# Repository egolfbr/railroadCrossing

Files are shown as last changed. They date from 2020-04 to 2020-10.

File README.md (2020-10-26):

# RailRoadCrossing
Arduino based railroad crossing replica 
## Table of Contents
## Table of Contents
**[Introduction](#Introduction)**<br>
**[Gather Materials](#Gather-Matierals)**<br>
**[Building](#Building)**<br>
**[Programming](#Programming)**<br>
**[Conclusion](#Conclusion)**<br>

## Introduction
With the coronavirus sending students home for the rest of the semester (spring 2020), I found myself with a lot of extra time on my hands and lots of parts that I have never used.I recalled that the theme for this years VBS at my church is a railroad theme and my idea was born. I decided that I was going to make a railroad crossing signal. You know the ones with the moving arm, sound and blinking lights. It seemed a little easy especially since I am a junior electrical engineering student so I set off to work, needless to say, I encountered many errors and problems that made this a not an “easy” project. Certainly not a “plug and go” anyway lets get started.

## Gather Materials
Step 1: Gather materials. 
* 3x Arduino UNOs - $23/ea (arduino.cc)
* 2x microswitches - $2/ea* (microcenter)
* 2x pushbuttons - $0.10/ea (digikey)
* 2x 8Ohm-1W speakers - $2.95/ea (microcenter)
* 1x adafruit sound effects board $30/ea (adafruit)
* 2x neopixel ring (16LEDs)
* 1x barrel jack
* 1x 5V 3A power supply
* 2x 10K ohm resistors
* Jumper wire
* 2x MOSFET N-ch 30V transistor
* 2x MOSFET P-ch 27A transistor
* 1x 555 timer
* 1x 125V 3A fuse
* 2x 10000pf ceramic capacitor
* 2x 1n4004 diode
* 1x 19rpm economy brush pur motor
* 1x 4mm shaft mount 32 pitch 16T gear
* 1x 32 pitch 64T 1” bore gear

Estimated total cost:
	For those who do not have any previous material the estimated total cost is about $276. This does not include shipping and tax as you will most likely end up ordering from multiple different places. Websites such as Amazon may make it cheaper. I ended up spending just under $100 on parts that I didn’t have. PCB ordering is also not factored into this cost. I usually order PCBs from China. This means that I have to order a minimum of 10 boards per design. Thus with SeedStudio, I will have to pay around $5 for each design as well as shipping and tax for each one. I also included what the cost would be had I been contracted by a client to build this device. I used a simple google search of the median income of an electrical engineer to base my calculation for the per hour pay. 

You may be wondering why I use so many microcontrollers for a relatively simple process. I was limited by 2 main factors in this build, materials that I had, and money. Now, using 3 micro controllers seems like a costly thing to do and it is. However, I was lucky enough to receive a donation of parts last year which included about 10 arduinos. So having these extra controllers was a huge relief because it allowed me to make this project more parallel. In other words, I have multiple processes running at the same time across multiple devices. I will get into this more as I explain the circuit in the next section, but as some of you may guess, running certain processes takes time and if I want to say blink LEDs and move a motor at the same time, there will be a delay in the circuit. I may make a video example of what I am talking about for those who are confused. 
## Building 
Step 2: build the circuit.
	The most important thing to remember here is to CONNECT ALL GROUND PINS. Also pin numbers are arbitrary. There is no specific reason I choose any of the digital IO pins. The SDA and SCL pins however must remain on A4 and A5 respectively. There are other places to connect these pins on other versions of the arduino UNO but I like to use these pins because they are universal on the UNO models. 
	Additionally, due to my lack of knowledge in EAGLE I will attach hand drawn circuit schematics for parts of the circuit that parts aren’t readily available for on EAGLE so that you have them and I will work on updating the EAGLE file so that there is one complete schematic file that can be downloaded. On the hand-drawn circuits, any node names that are the same on the EAGLE file are connected. For example, on the board labeled SOUND, there is a pin labeled SOUNDPIN. On the hand-drawn schematic there is also a SOUNDPIN, that means that those nodes are connected. Also there is a portion of the circuit that is simplified. For the neopixel rings I only included 2xsingle LED schematics. In reality each of those single LEDs is a whole 16 LED ring. Connections are the same though because you are connecting the last LED on the first ring with the first LED on the second ring.
	So like I mentioned before, I chose to use multiple arduino so that I could make this a parallel design. The other option for me would be to use an FPGA since those are much easier to parallelize however, I did not have the equipment to debug that device. So that is why I ended up with lots of arduinos. First I was planning on just using two arduinos but found that trying to quickly change cases in the state machine (the code implementation that I will discuss next), this proved too slow. This is because in the code I called a function to flash the neopixel LEDs and this takes time. 
Let me take a break here and explain why I chose neopixel rings. Realistically I would’ve used lots of small 3-5mm LEDs and not these rings. That is because with the single diodes, you can simply connect and disconnect power to blink the LEDs. This would lead me to do a hardware implementation of the blinking lights. This can be done a couple ways. I saw a way to do it with a switching NPN transistor similar to the 2n2222 (please correct me if I am wrong). I imagine that this can be done with a crystal oscillator or a 555 timer circuit. I did have several 555 timers available to use but unfortunately I only had about 20 THT LEDs. So that is the main reason that I used the rings. I also find the rings brighter. The big downside is that they must remain plugged into the programmed pin (in my case pin 6). 
Okay so I grabbed a new arduino so that I could put a dedicated LED flashing code on it to flash during 3 of the 4 states of the state machine. Even though this one arduino is slower than the rest in terms of reading/displaying data on the SDA line, it is more acceptable because little kids love LEDs and who cares if the LEDs are on for a second or 2 longer than necessary. It is much more desirable and safer than say having the master arudino not read the digital pins while the motor is still running trying to push the arm higher and stalling the motor and maybe causing a fire. 
For the sound arduino I used the Adafruit sound effects board and some low powered speakers. This was the plug and go part of the project. There is a tutorial on how to use this board on Adafruit’s website which I will post a link to. The sound file is a simple MP3 that I downloaded for free (link below). You don’t have to include a sound portion to this project as it does get rather annoying but I always enjoy sound effects.
For the motor I just used the sound arduino because the sound doesn’t take a lot of time because it is just toggling a pin high and low. I used an attached link for the build of a custom H-bridge motor driver with variable speed and direction. The attached link had 95% of the circuit already designed so that was very helpful. The only portion that I personally designed and built was making it “programmable.” This means that instead of using a physical switch to change direction and to power the motor on and off, I used signals from the arduino dedicated to that function. The main issue is that I needed a SPDT switch that doesn’t require human interaction. Again, limited by supplies I landed on a 5V relay. A relay can be used similar to a 2n2222 transistor in that it can control higher voltage and amperage signals with a common 5V or 3.3V signal depending on the relay. In this case I didn’t need it to control a high voltage or current, just the fact that I needed it to be programmable. So the relay portion of the circuit controls the direction because for an H-bridge, if one side is connected to the power supply, and the other side is at ground, then the motor spins one way and if you switch those signals then you can make it spin the other way. To control the status of the motor (whether it is on or off) I simply used another N-Channel MOSFET transistor. Below are some images of the full circuit. First is the full motor dirver all wired up with a PWM signal and Hbridge, then just the PWM signal generator (555 timer circuit), then the master controller which takes inputs from sensors and buttons, the LED circuit which is just some neoPixel Rings, and finally, the audio circuit. I used an Adafruit sound effects board to shorten the project and bring the complexity down a bit.
<p align="center">
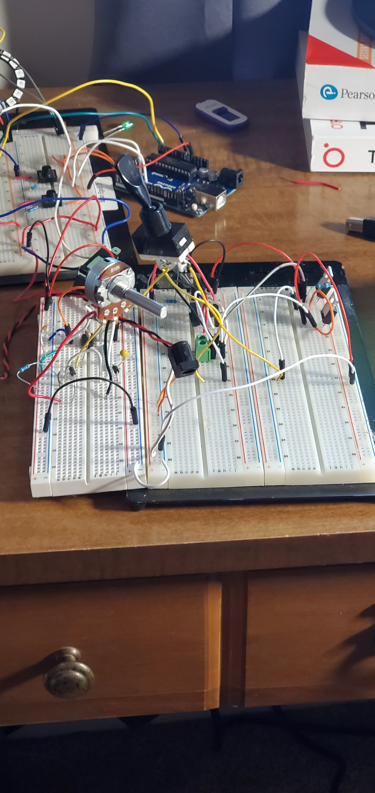
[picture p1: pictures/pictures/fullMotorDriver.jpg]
	
	
<p align="center">
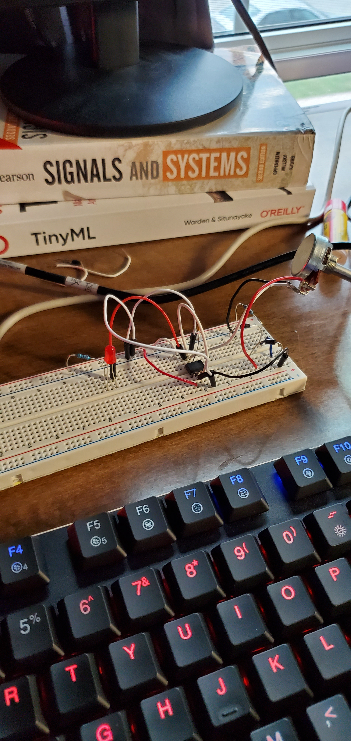
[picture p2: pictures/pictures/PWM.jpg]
		

<p align="center">
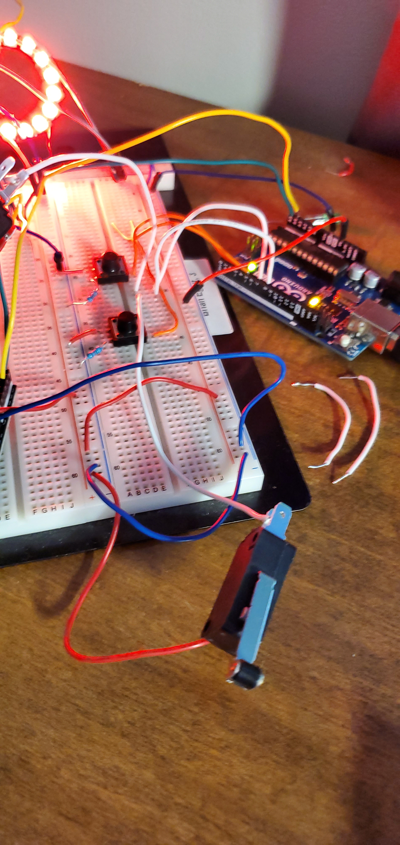
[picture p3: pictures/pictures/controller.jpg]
		

<p align="center">
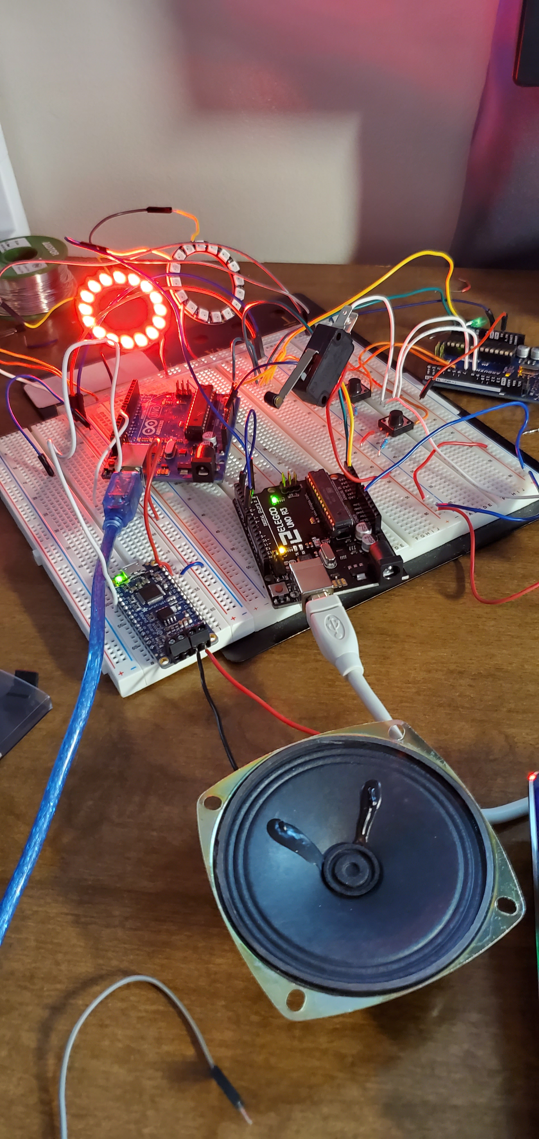
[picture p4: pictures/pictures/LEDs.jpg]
		

<p align="center">
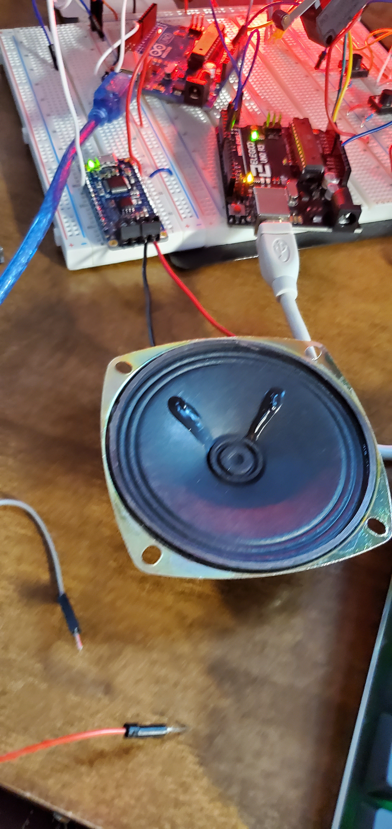
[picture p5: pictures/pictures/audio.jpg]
	

## Programming
Step 3: Code the Arduino’s
	For this project I implemented a state machine. This is just so that it is easier to organize on paper, in the code and in my head. Basically a state machine is a machine whose outputs are decided by which state it is in and the state is decided by the inputs. That is just a very general description. State machines are all around us from traffic lights to elevators, so it is very useful to get to know how to program one and how they work. Typically, these are implemented with an FPGA but they can really be implemented with anything. My code is heavily commented so I don’t anticipate this to be a long section. 

State Diagram:

<p align="center">
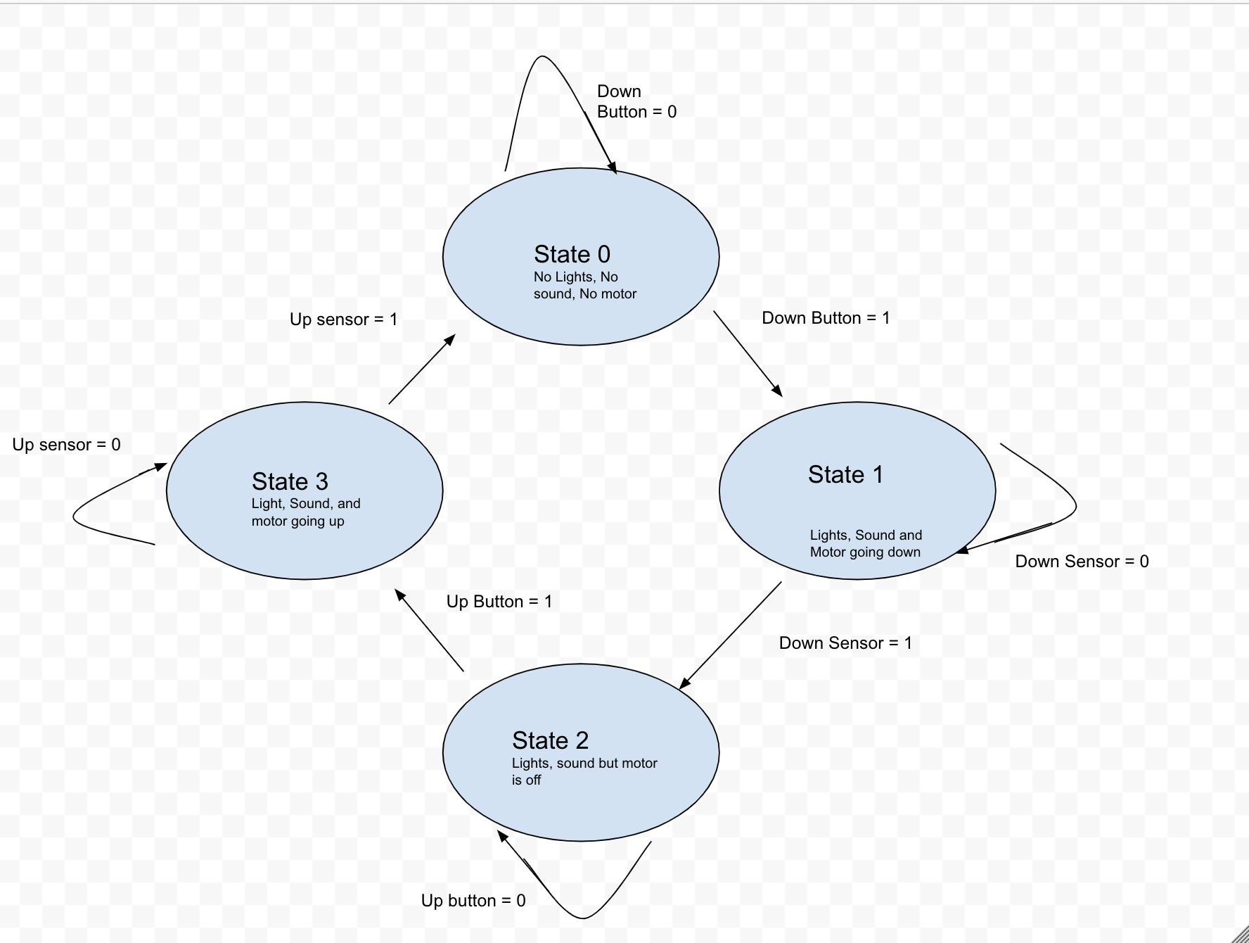
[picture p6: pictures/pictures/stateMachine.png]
	

The state diagram helps visualize what is supposed to happen. This helps when errors occur etc.  
A key note that I found out debugging my code is that the break statements are very important when using switch statements. Without these the code won’t run properly. I tried to do some basic research on the switch statements because I had used switch statements before but I had not looked into why we use breaks. What I came up with was that breaks basically prevent the code from running the following case.

## Conclusion

Overall this project took me about 12 hours to complete. I worked for about 2-3 hrs every couple days or so for about 3 weeks. However, if you had all the parts I imagine that this would take maybe an afternoon or two. The main thing that slowed me down were simple software errors mainly. The hardware was rather simple once I got the parts. There were a few instances where I had to improvise and come up with some of my own stuff (see motor power and motor direction without buttons) but again most of the information was already available I just had to synthesize it in a certain way. If I were to do this again  I would try to implement this with an FPGA and more hardware solutions like the 555 timer circuit for the LEDs. I would like to print PCBs for this project to make it more professional as well. Furthermore I would like to see if there is a way to use less arduinos. The one thing that I will probably actually do as an extension is that I will add another arduino or raspberry pi to read telemetry data from the circuit and based on that master data determine if it is necessary to shut the circuit off. I already need to wire battery packs to all the arduinos to a master switch to turn them all on  at the same time and having that switch or another controlled via microcontroller shouldn’t be too hard. I will also add a screen to display current information relevant to the well being of the circuit. 
	
video link: https://youtu.be/l8aVLoQLqr0

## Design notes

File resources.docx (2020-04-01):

Links to resources used in the project:

https://www.youtube.com/watch?v=LXGtE3X2k7Y - how to protect my relay and motor from inductive spikes

https://www.youtube.com/watch?v=iYafyPZ15g8 - motor driver circuit

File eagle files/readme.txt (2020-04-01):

    These files are free software: you can redistribute it and/or modify
    it under the terms of the GNU General Public License as published by
    the Free Software Foundation, either version 3 of the License, or
    (at your option) any later version.

    This program is distributed in the hope that it will be useful,
    but WITHOUT ANY WARRANTY; without even the implied warranty of
    MERCHANTABILITY or FITNESS FOR A PARTICULAR PURPOSE.  See the
    GNU General Public License for more details.

    You should have received a copy of the GNU General Public License
    along with this program.  If not, see <https://www.gnu.org/licenses/>.
    
    These eagle files were prototyped and designed by Brian Egolf.

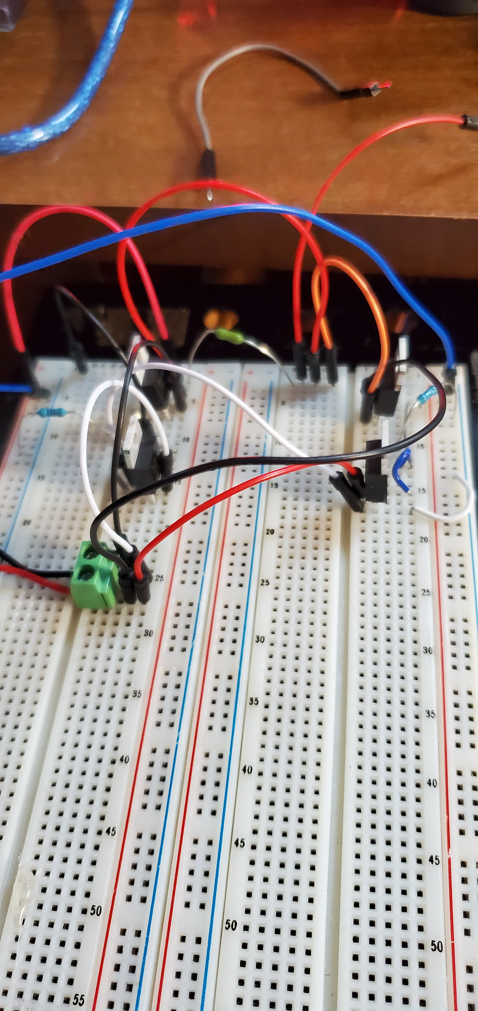
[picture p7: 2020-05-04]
pictures/pictures/Hbridge.jpg

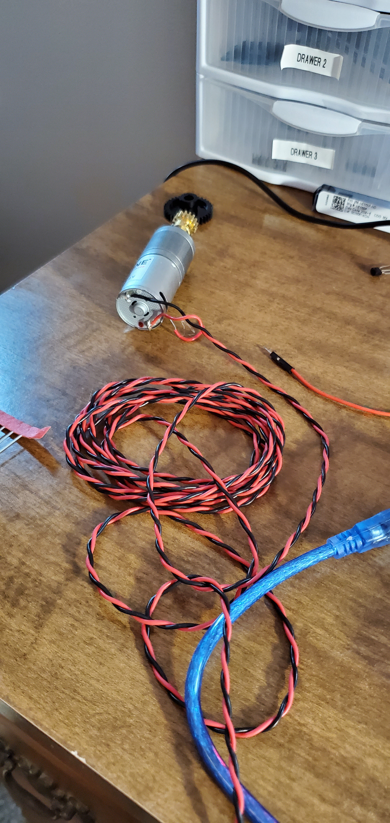
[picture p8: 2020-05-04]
pictures/pictures/motor.jpg

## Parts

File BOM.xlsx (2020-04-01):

item | quantity | cost | total | vendor
Arduino UNOs | 3 | $23 | $69 | Arduino.cc
microswitches - $2/ea* (microcenter) | 2 | $2 | $4 | microcenter.com
pushbuttons - $0.10/ea (digikey) | 2 | $0.10 | $0.20 | digikey.com
8Ohm-1W speakers - $2.95/ea (microcenter) | 2 | $2.95 | $5.90 | microcenter.com
adafruit sound effects board $30/ea (adafruit) | 1 | $30 | $30 | adafruit.com
neopixel ring (16LEDs) | 2 | $9.95 | $19.90 | adafruit.com
barrel jack | 1 | $0.95 | $0.95
5V 3A power supply (or 4A) | 1 | $14.95 | $14.95
10K ohm resistors | 4 | $0.10 | $0.40 | digikey.com
1k ohm resistor | 2 | $0.10 | $0.20 | digikey.com
330 ohm resistor | 3 | $0.10 | $0.30 | digikey.com
47 ohm resistor | 1 | $0.10 | $0.10 | digikey.com
Jumper wire | 1 | $19.95 | $19.95 | https://www.adafruit.com/
12 ft carpet tude | 1 | $0 | $0 | Usually will be provided for free by a local carpet store
6ft pool noodle | 1 | $6.99 | $6.99 | https://foamnoodles.com/
6ft PVC pipe ½” diameter | 1 | $2.98 | $2.98 | home depot
empty paint can | 2 | $2.97 | $5.94 | home depot
Black paint | 2 | $3.98 | $7.96 | home depot
Grey paint | 2 | $3.98 | $7.96 | home depot
Red paint | 2 | $3.98 | $7.96 | home depot
White paint | 2 | $3.98 | $7.96 | home depot
2”x1/4” x3’ pieces of wood | 2 | $13.69 | $27.38 | home depot
MOSFET N-ch 30V transistor | 2 | $0.76 | $1.52 | digikey.com
MOSFET P-ch 27A transistor | 2 | $1.41 | $2.82 | digikey.com
555 timer | 1 | $0.45 | $0.45 | digikey.com
125V 3A fuse | 1 | $0.85 | $0.85 | digikey.com
10000pf ceramic capacitor | 2 | $0.23 | $0.46 | digikey.com
1n4004 diode | 2 | $0.11 | $0.22 | digikey.com
19rpm economy brush pur motor | 1 | $14.99 | $14.99 | servocity.com
4mm shaft mount 32 pitch 16T gear | 1 | $7.99 | $7.99 | servocity.com
32 pitch 64T 1” bore gear | 1 | $5.29 | $5.29 | servocity.com
Labor/hr | 12 | $45.80 | $549.60 | **
total parts |  |  | $275.57
net total |  |  | $825.17
* estimated value
** based on median income of electrical engineer in the US.

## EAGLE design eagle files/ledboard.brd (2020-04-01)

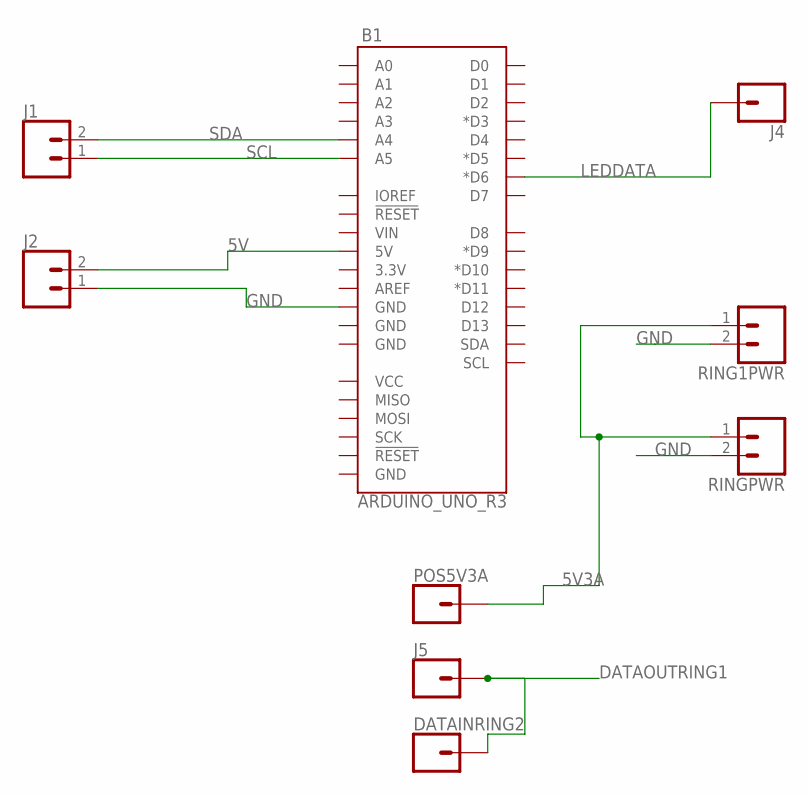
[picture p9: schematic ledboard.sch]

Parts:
B1: ARDUINO_UNO_R3; ARDUINO_R3
DATAINRING2: CONN_01; 1X01
J1, J2: CONN_023.5MM; SCREWTERMINAL-3.5MM-2
J4, J5: CONN_01; 1X01
POS5V3A: CONN_01; 1X01
RING1PWR: CONN_023.5MM; SCREWTERMINAL-3.5MM-2
RINGPWR: CONN_023.5MM; SCREWTERMINAL-3.5MM-2

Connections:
5V: B1.5V, J2.2
5V3A: POS5V3A.1, RING1PWR.1, RINGPWR.1
DATAOUTRING1: DATAINRING2.1, J5.1
GND: B1.GND@4 (GND), J2.1, RING1PWR.2, RINGPWR.2
LEDDATA: B1.D6 (*D6), J4.1
SCL: B1.A5, J1.1
SDA: B1.A4, J1.2

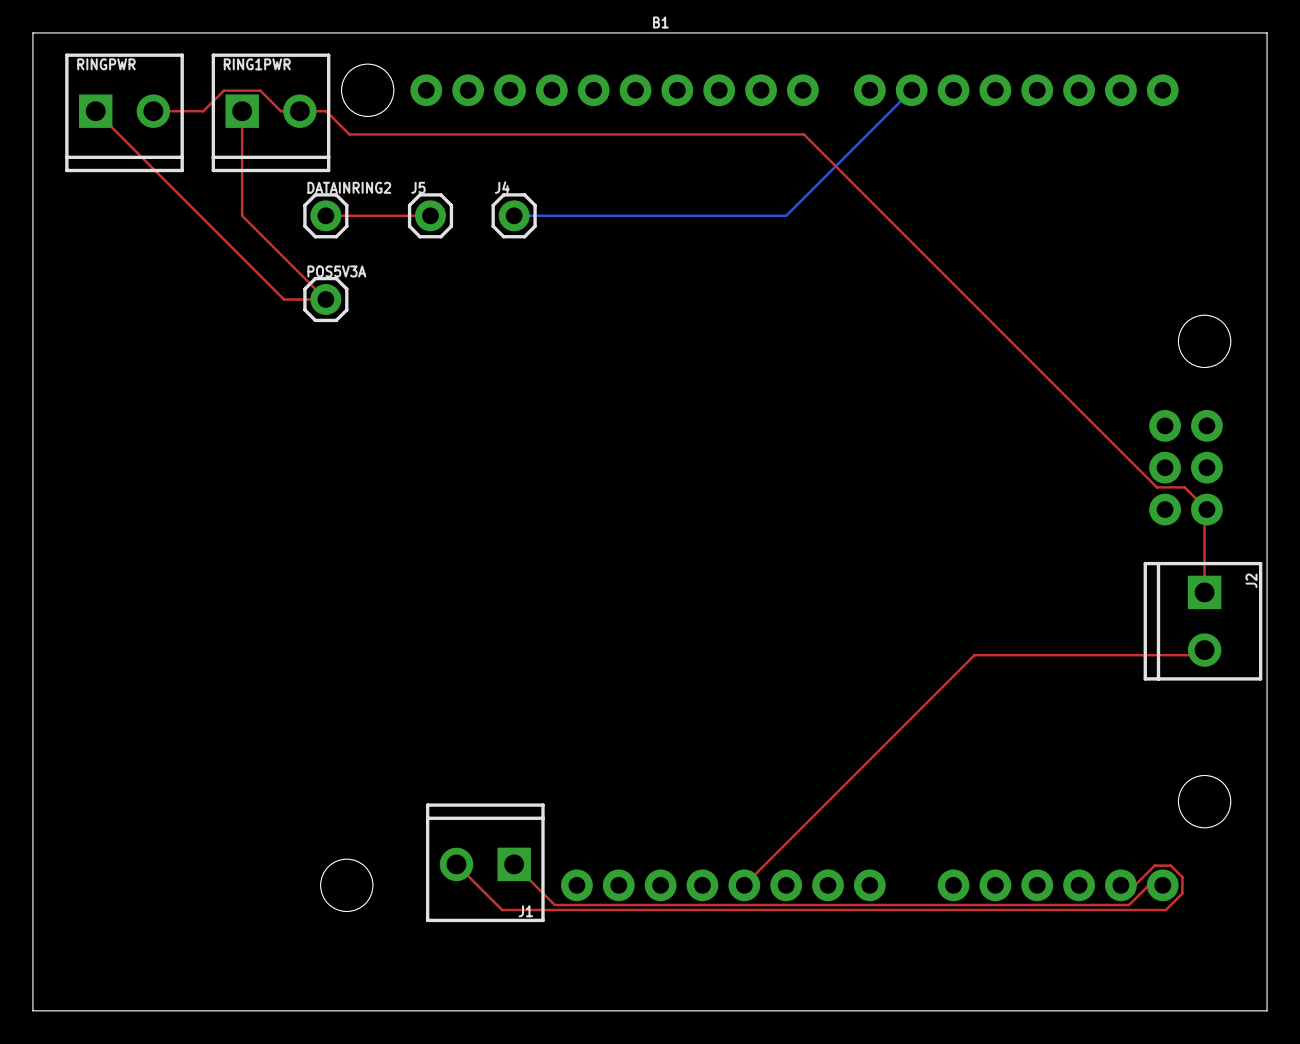
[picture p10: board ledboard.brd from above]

Board: 2 copper layers, 74.9 x 59.4 mm, 9 parts (0 on the bottom side), 7 nets.

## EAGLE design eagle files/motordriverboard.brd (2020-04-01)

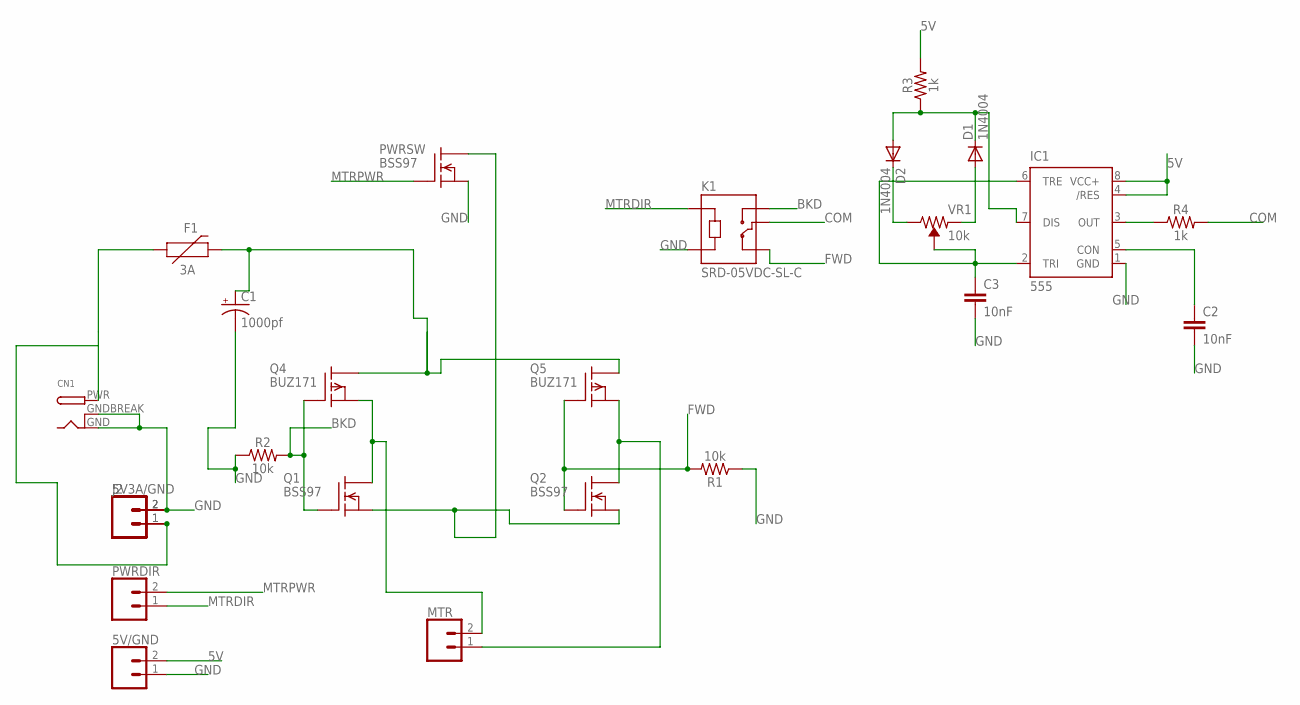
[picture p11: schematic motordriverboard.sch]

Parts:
5V3A/GND, 5V/GND: CONN_023.5MM; SCREWTERMINAL-3.5MM-2
C1: 1000pf; E5-6
C2, C3: 10nF; CAP-PTH-10MM
CN1: DCBARRELPTH; DCJACK_2MM_PTH
D1, D2: 1N4004; DO41-10
F1: 3A; PTH
IC1: 555; DIP08
J2: CONN_023.5MM; SCREWTERMINAL-3.5MM-2
K1: SRD-05VDC-SL-C; RELAY_SRD-05VDC-SL-C
MTR: CONN_023.5MM; SCREWTERMINAL-3.5MM-2
PWRDIR: CONN_023.5MM; SCREWTERMINAL-3.5MM-2
PWRSW: BSS97; TO202
Q1, Q2: BSS97; TO202
Q4, Q5: BUZ171; TO220
R1, R2: 10k; AXIAL-0.3
R3, R4: 1k; AXIAL-0.3
VR1: 10k; TRIMPOT-PTH-3386U

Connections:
5V: 5V/GND.2, IC1.4 (/RES), IC1.8 (VCC+), R3.P$2 (2)
BKD: K1.NO, Q1.3 (G), Q4.1 (G), R2.P$2 (2)
COM: K1.COM, R4.P$2 (2)
FWD: K1.NC, Q2.3 (G), Q5.1 (G), R1.P$2 (2)
GND: 5V3A/GND.2, 5V/GND.1, C1.-, C2.2, C3.2, CN1.GND, CN1.GNDBREAK, IC1.1 (GND), J2.2, K1.A2, PWRSW.1 (S), R1.P$1 (1), R2.P$1 (1)
MTRDIR: K1.A1, PWRDIR.1
MTRPWR: PWRDIR.2, PWRSW.3 (G)
unnamed: C2.1, IC1.5 (CON)
unnamed: IC1.3 (OUT), R4.P$1 (1)
unnamed: C3.1, IC1.2 (TRI), IC1.6 (TRE), VR1.2 (WIPER)
unnamed: C1.+, F1.P$2 (2), Q4.2 (D), Q5.2 (D)
unnamed: D1.C, D2.A, IC1.7 (DIS), R3.P$1 (1)
unnamed: MTR.1, Q2.2 (D), Q5.3 (S)
unnamed: MTR.2, Q1.2 (D), Q4.3 (S)
unnamed: PWRSW.2 (D), Q1.1 (S), Q2.1 (S)
unnamed: 5V3A/GND.1, CN1.PWR, F1.P$1 (1), J2.1
unnamed: D2.C, VR1.3 (CW)
unnamed: D1.A, VR1.1 (CCW)

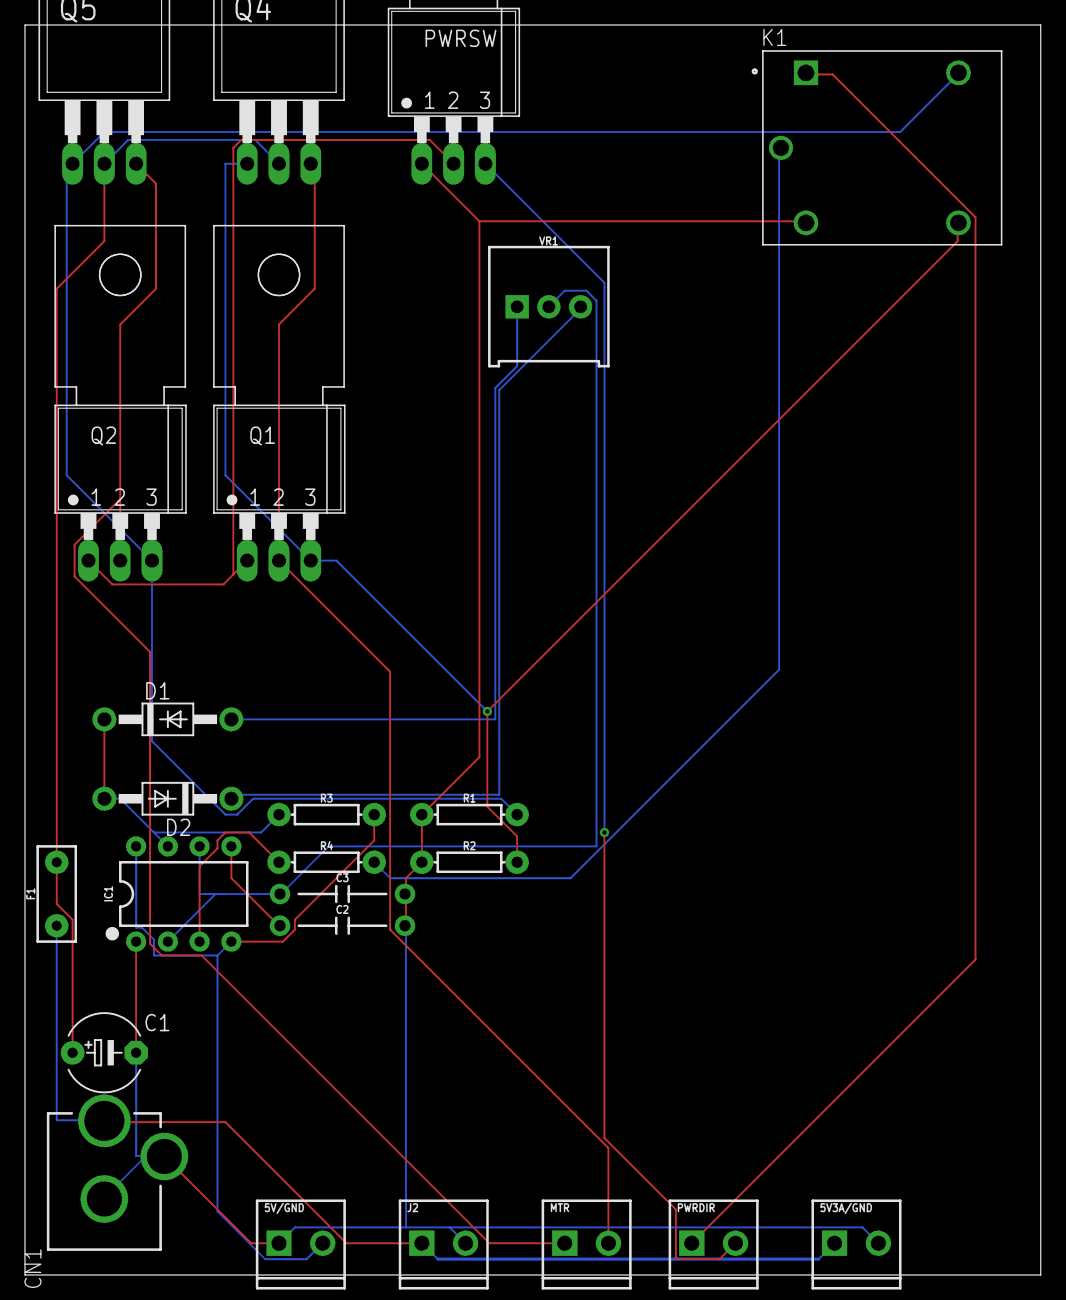
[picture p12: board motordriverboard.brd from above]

Board: 2 copper layers, 81.3 x 100.0 mm, 24 parts (0 on the bottom side), 18 nets.

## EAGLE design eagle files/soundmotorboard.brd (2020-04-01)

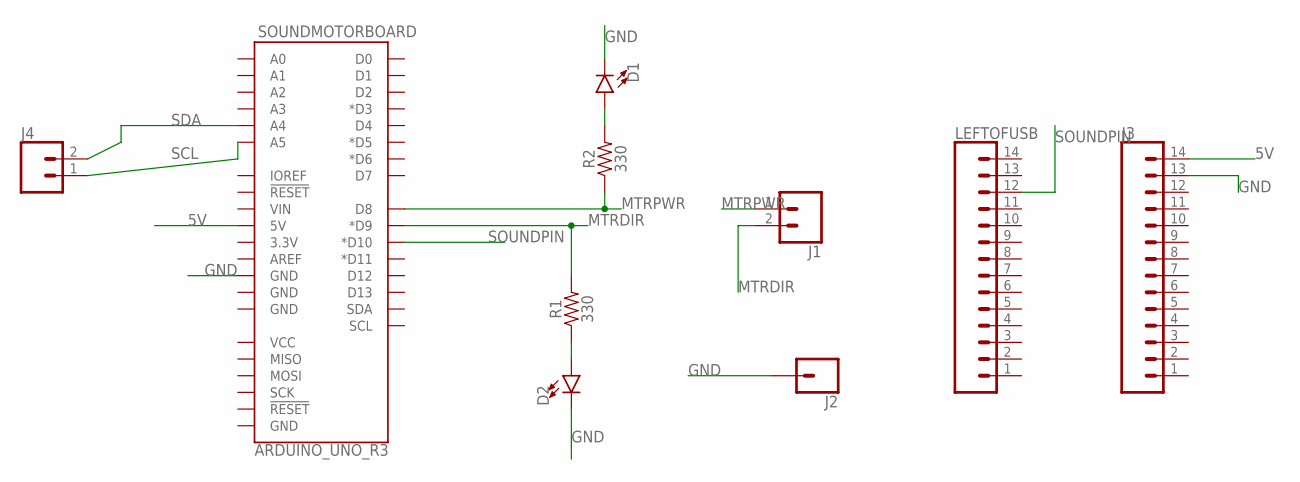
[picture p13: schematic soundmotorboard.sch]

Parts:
D1, D2: LED5MM; LED_5MM
J1: CONN_023.5MM-NO_SILK; SCREWTERMINAL-3.5MM-2-NS
J2: CONN_01; 1X01
J3: CONN_14; 1X14
J4: CONN_023.5MM; SCREWTERMINAL-3.5MM-2
LEFTOFUSB: CONN_14; 1X14
R1, R2: 330; AXIAL-0.3
SOUNDMOTORBOARD: ARDUINO_UNO_R3; ARDUINO_R3

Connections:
5V: J3.14, SOUNDMOTORBOARD.5V
GND: D1.K (C), D2.K (C), J2.1, J3.13, SOUNDMOTORBOARD.GND@4 (GND)
MTRDIR: J1.2, R1.P$2 (2), SOUNDMOTORBOARD.D9 (*D9)
MTRPWR: J1.1, R2.P$1 (1), SOUNDMOTORBOARD.D8
unnamed: D1.A, R2.P$2 (2)
unnamed: D2.A, R1.P$1 (1)
SCL: J4.1, SOUNDMOTORBOARD.A5
SDA: J4.2, SOUNDMOTORBOARD.A4
SOUNDPIN: LEFTOFUSB.12, SOUNDMOTORBOARD.D10 (*D10)

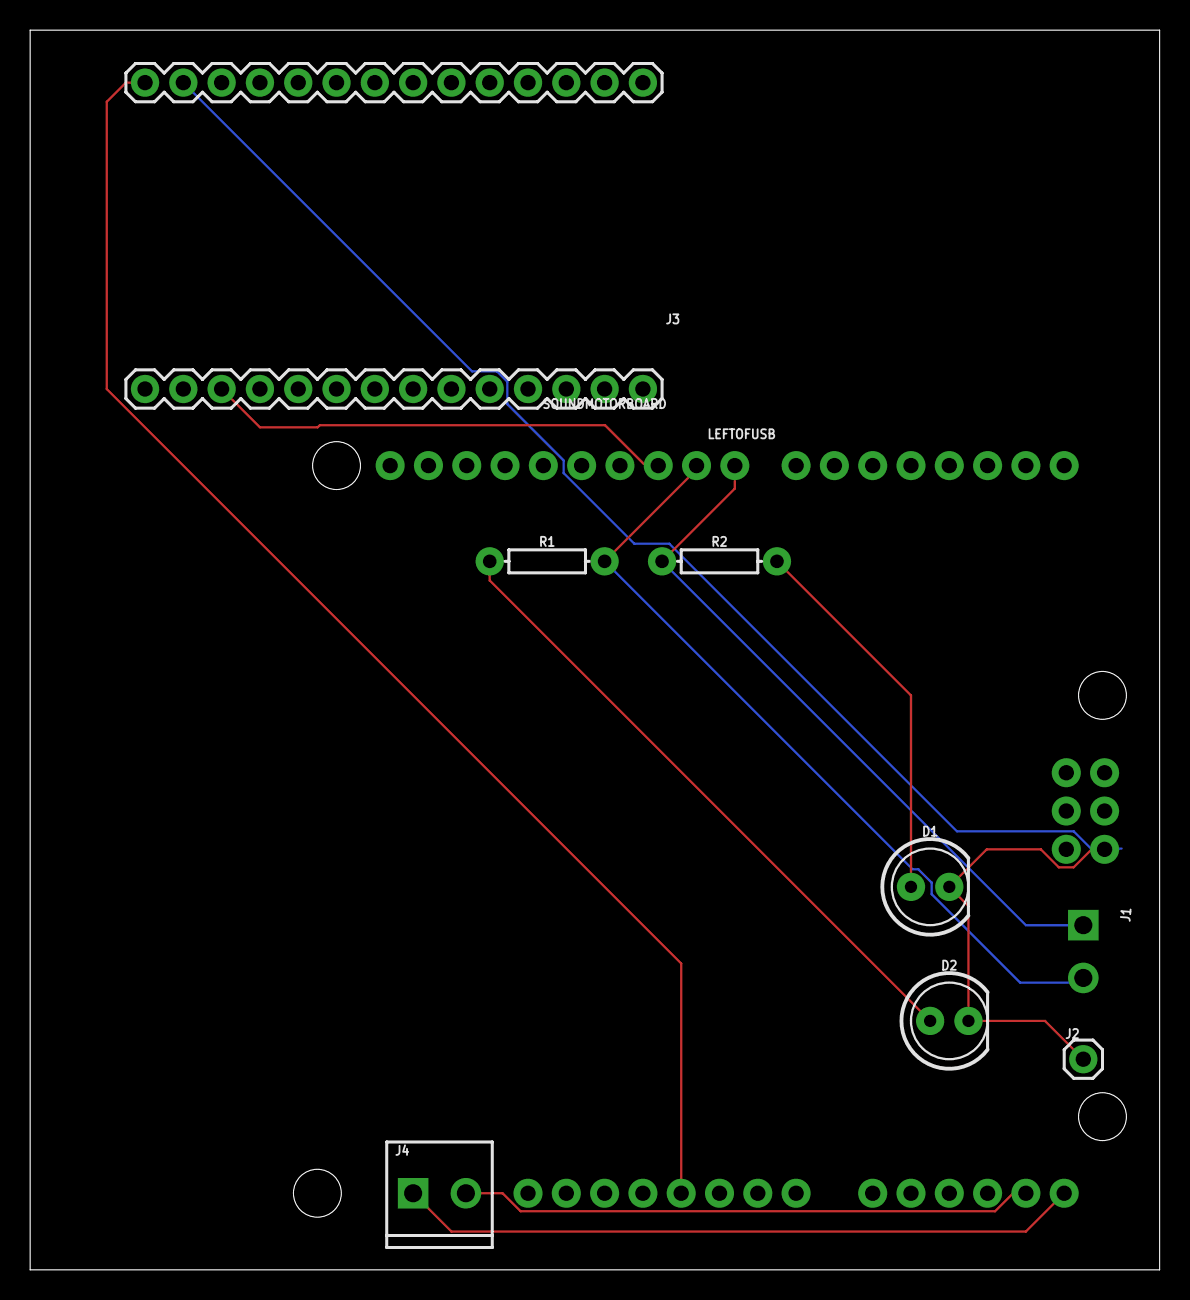
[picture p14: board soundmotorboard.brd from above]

Board: 2 copper layers, 74.9 x 82.2 mm, 10 parts (0 on the bottom side), 9 nets.

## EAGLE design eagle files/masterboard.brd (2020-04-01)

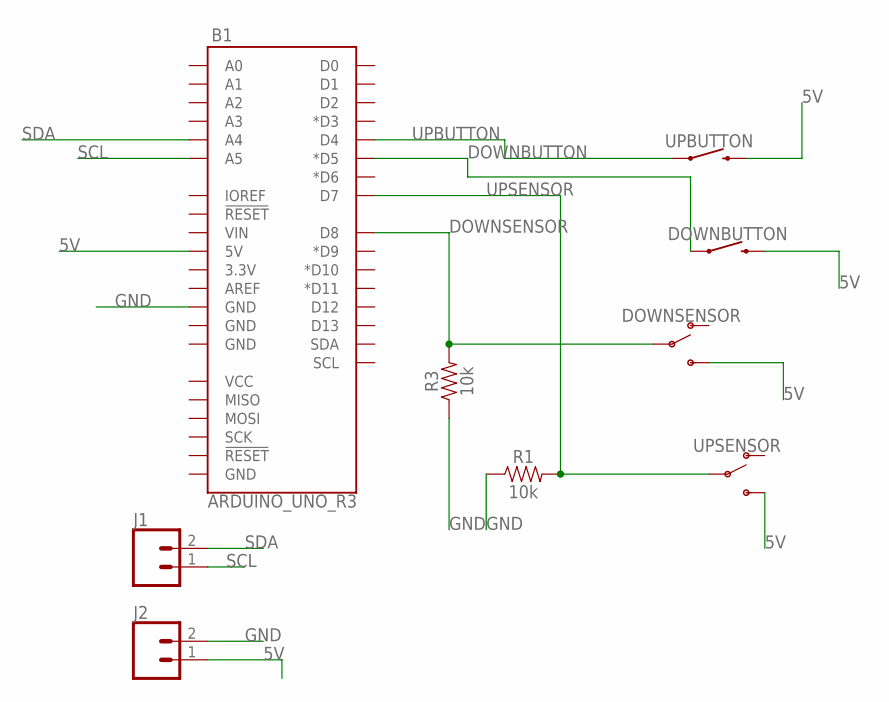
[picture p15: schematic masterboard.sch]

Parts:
B1: ARDUINO_UNO_R3; ARDUINO_R3
DOWNBUTTON: MOMENTARY-SWITCH-SPST-PTH-6.0MM-KIT; TACTILE_SWITCH_PTH_6.0MM_KIT
DOWNSENSOR: SWITCH-SPDT-PTH-11.6X4.0MM; SWITCH_SPDT_PTH_11.6X4.0MM
J1, J2: CONN_023.5MM; SCREWTERMINAL-3.5MM-2
R1, R3: 10k; AXIAL-0.3
UPBUTTON: MOMENTARY-SWITCH-SPST-PTH-6.0MM-KIT; TACTILE_SWITCH_PTH_6.0MM_KIT
UPSENSOR: SWITCH-SPDT-PTH-11.6X4.0MM; SWITCH_SPDT_PTH_11.6X4.0MM

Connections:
5V: B1.5V, DOWNBUTTON.3 (2), DOWNSENSOR.3 (S), J2.1, UPBUTTON.3 (2), UPSENSOR.3 (S)
DOWNBUTTON: B1.D5 (*D5), DOWNBUTTON.1
DOWNSENSOR: B1.D8, DOWNSENSOR.2, R3.P$2 (2)
GND: B1.GND@4 (GND), J2.2, R1.P$1 (1), R3.P$1 (1)
SCL: B1.A5, J1.1
SDA: B1.A4, J1.2
UPBUTTON: B1.D4, UPBUTTON.1
UPSENSOR: B1.D7, R1.P$2 (2), UPSENSOR.2

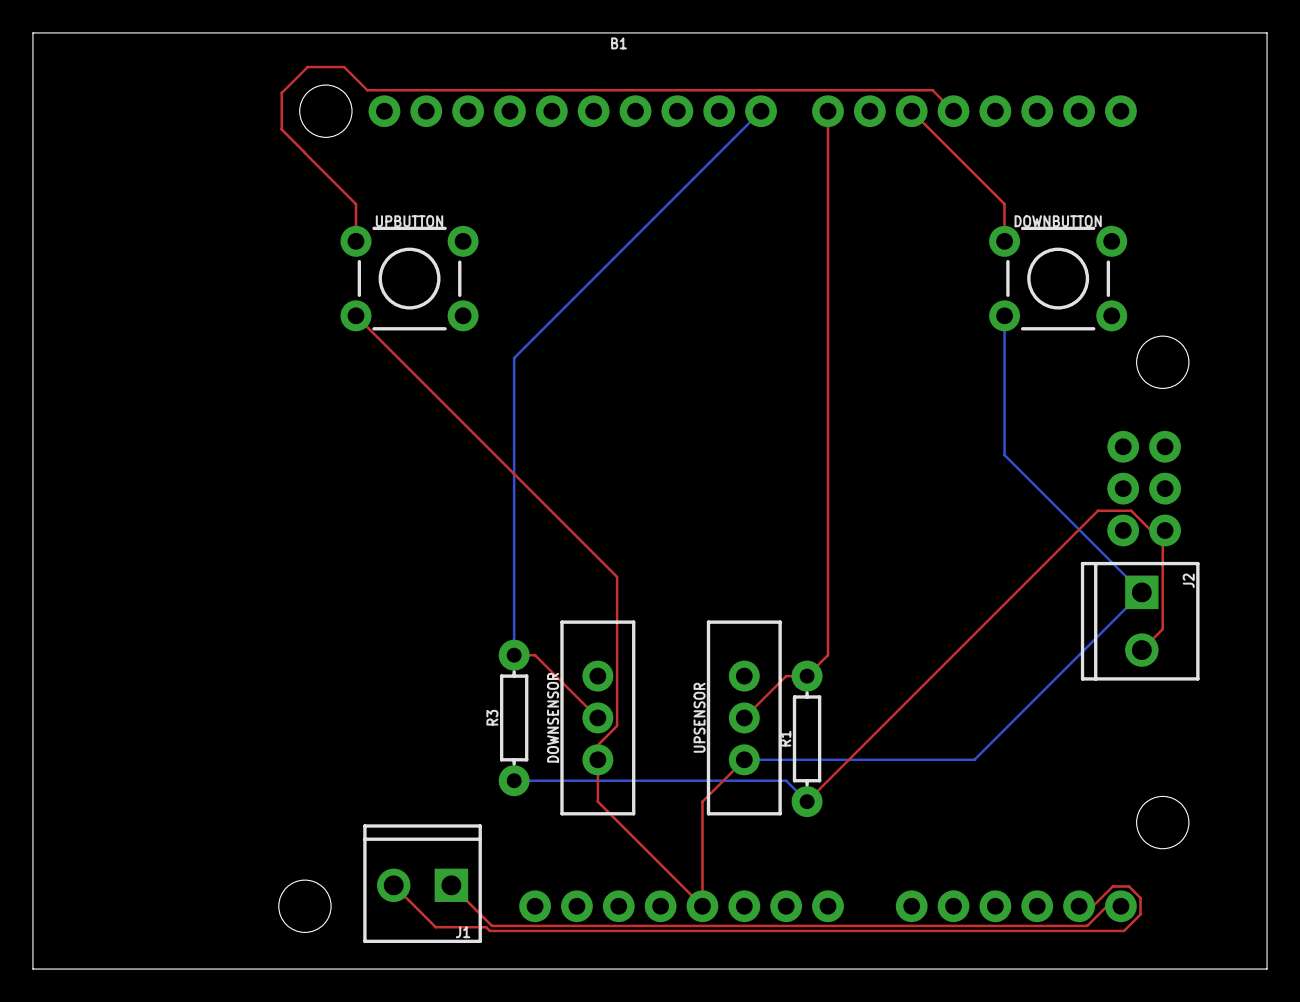
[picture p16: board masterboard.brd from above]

Board: 2 copper layers, 74.9 x 56.8 mm, 9 parts (0 on the bottom side), 8 nets.

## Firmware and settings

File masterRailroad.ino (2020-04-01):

/*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
*/

//master for the railroad crossing implemented as a state machine

//libraries that this arduino will use in the machine
#include <Wire.h>
#include <Adafruit_NeoPixel.h>

// On a Trinket or Gemma we suggest changing this to 1:
// This is the pin that the DATA_IN pin is connected to on the first ring
#define LED_PIN    6

// How many NeoPixels are attached to the Arduino?
#define LED_COUNT 32

//must declare the strip using the built in declaration statement
Adafruit_NeoPixel strip(LED_COUNT, LED_PIN, NEO_GRB + NEO_KHZ800);

//sensor pins, these are attached to the physical build of the device to sense when the arm is either up or down
int upSensor = 7;
int downSensor = 8;

//buttons for state transition, these will determine if the arm will go up or down depending on which state the machine is in
//for example, if we are in state 0 and the up button is pressed, it won't do anything, but if the down button is pressed then we change states
int upButton = 4;
int downButton = 5;

//vars to store state of the above buttons
int buttonStateUp;
int buttonStateDown;

//comflag to tell if we have already communicated with the other device without a state transition
int comflag = 0;

//to tell the previous states of the machine 
int prevState = 0;

//state var for switch case
int mode = 0;
/*
 * for reference in the switch case here are the following states and the corressponding numbers
 * Start = 0: this is the default start case where the arm is up and the LEDs are off (no train)
 * Move down/flash = 1: this is the state where the arm is moving down and the LEDs are flashing (incoming train)
 * flash (sound?) = 2: this is where the arm has completed its movement and the LEDs are flashing (train is passing)
 * move up/flash = 3: this is the state where the arm moves back up and the LEDs are still flashing
 * 
 * Note: I only commented on the first case since the cases are mostly the same
 */


void setup() {
//begin the I2C communication  protocol
Wire.begin();
//defining the inputs and outputs of the system
pinMode(upButton, INPUT);
pinMode(downButton, INPUT);
pinMode(upSensor, INPUT);
pinMode(downSensor, INPUT);
//begin the serial communication protocol for debugging
Serial.begin(9600);
//start the strip
strip.begin();
strip.show();
}

//byte to send of the I2C communication line
byte x = 0;

void loop() {
//read state of the buttons
  buttonStateDown = digitalRead(downButton);

  //state machine portion. This will determine the output of the I2C data line which will be read by the slave 
  switch(mode) {
    case 0:
    //clear the LEDs 
    clearLeds();
    //tell whether we have communicated with the other boards since we have been in this state
      if(prevState != mode){
        //actually send the data to the slaves
          sendData(mode);
      }

      //determine if the button is pressed
      if(buttonStateDown == HIGH){
        //if the button is pressed then we update the prevState to the current state and then change the mode
        prevState = mode;
        mode = 1;
      }
      else{
        //update the prevState and mode
        prevState = mode;
        mode = 0;
        //switch case will not work properly without this break statement         
       break;
      }
    case 1:
      if(prevState != mode){
          sendData(mode);
      }
      if(digitalRead(downSensor) == HIGH){
        prevState = mode;
        mode = 2;
        
      }
      else{        
        prevState = mode;
        mode = 1;
        break;
      }
    case 2:
     buttonStateUp = digitalRead(upButton);
     if(prevState != mode){
          sendData(mode);
        }
      if(buttonStateUp == HIGH){
        prevState = mode;
        mode = 3;
        
      }
      else{
        
        prevState = mode;
        mode = 2;
        break;
      }
    case 3:
    if(prevState != mode){
          sendData(mode);
    }
    if(digitalRead(upSensor) == HIGH){
      prevState = mode;
      comflag = 0;
      mode = 0;
    }
    else{
      prevState = mode;
      mode = 3;         
      break;
    }
  }

}

void clearLeds(){
   for(int a =0;a<=32;a++){
        strip.setPixelColor(a, strip.Color(0,0,0));
      }
      strip.show();
}

int sendData(byte stateNum){
  //begin wire transmisison to the given address
  Wire.beginTransmission(8);
  //send the state number to the slave
  Wire.write(stateNum);
  //end the transmission
  Wire.endTransmission();
  //begin transmission to the other slave
   Wire.beginTransmission(4);
  Wire.write(stateNum);
  Wire.endTransmission();
  //display when we have sent the data.
  Serial.println("Sent data to slave(s)");
}

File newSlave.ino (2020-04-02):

/*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
*/


//slave 1. This device controls the motor power, motor direction and the sound.
#include <Wire.h>

int motorPin = 9;
int soundPin = 10;
int motorPwr = 8;
int y;
int soundFlag = 0;

void setup() {
pinMode(motorPin, OUTPUT);
pinMode(motorPwr,OUTPUT);
pinMode(soundPin, OUTPUT);

Wire.begin(8);
Wire.onReceive(receivedEvent);
Serial.begin(9600);

}

void loop() {
  Serial.println(y);
switch(y){
  
  case 0:
   //motor off nothing is happening

   motorOff(motorPwr);
   if(soundFlag == 0){
    digitalWrite(soundPin, HIGH);
   }
  if(soundFlag == 1){
  soundOff(soundPin);
  soundFlag = 0;
   }
  break;
   
  case 1:
    //motor on down

   motorOn(motorPwr);
   mDown(motorPin);

  soundOn(soundPin);
  soundFlag = 1;

  break;
  
  case 2:
    //motor off


   motorOff(motorPwr);


   break;
  case 3:
    //motor on up 
   motorOn(motorPwr);
   mUp(motorPin);
   break;
  }
  
}

void receivedEvent(int howMany){
  int x = Wire.read();
  y = x;
}
void motorOff(int mtrPwr){
  digitalWrite(mtrPwr, LOW);
}
void soundOff(int pinNum){
  digitalWrite(pinNum, HIGH);
  delay(10);
  digitalWrite(pinNum,LOW);
  delay(10);
}
void motorOn(int mtrPwr){
  digitalWrite(mtrPwr, HIGH);
}
void soundOn(int pinNum){
  digitalWrite(pinNum, LOW);
}
void mUp(int motorPin){
  digitalWrite(motorPin, LOW);
}
void mDown(int motorPin){
  digitalWrite(motorPin, HIGH);
}

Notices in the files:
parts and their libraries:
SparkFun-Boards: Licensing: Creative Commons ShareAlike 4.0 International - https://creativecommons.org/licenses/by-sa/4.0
